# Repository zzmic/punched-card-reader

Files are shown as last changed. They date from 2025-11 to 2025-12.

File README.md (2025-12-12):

# punched-card-reader
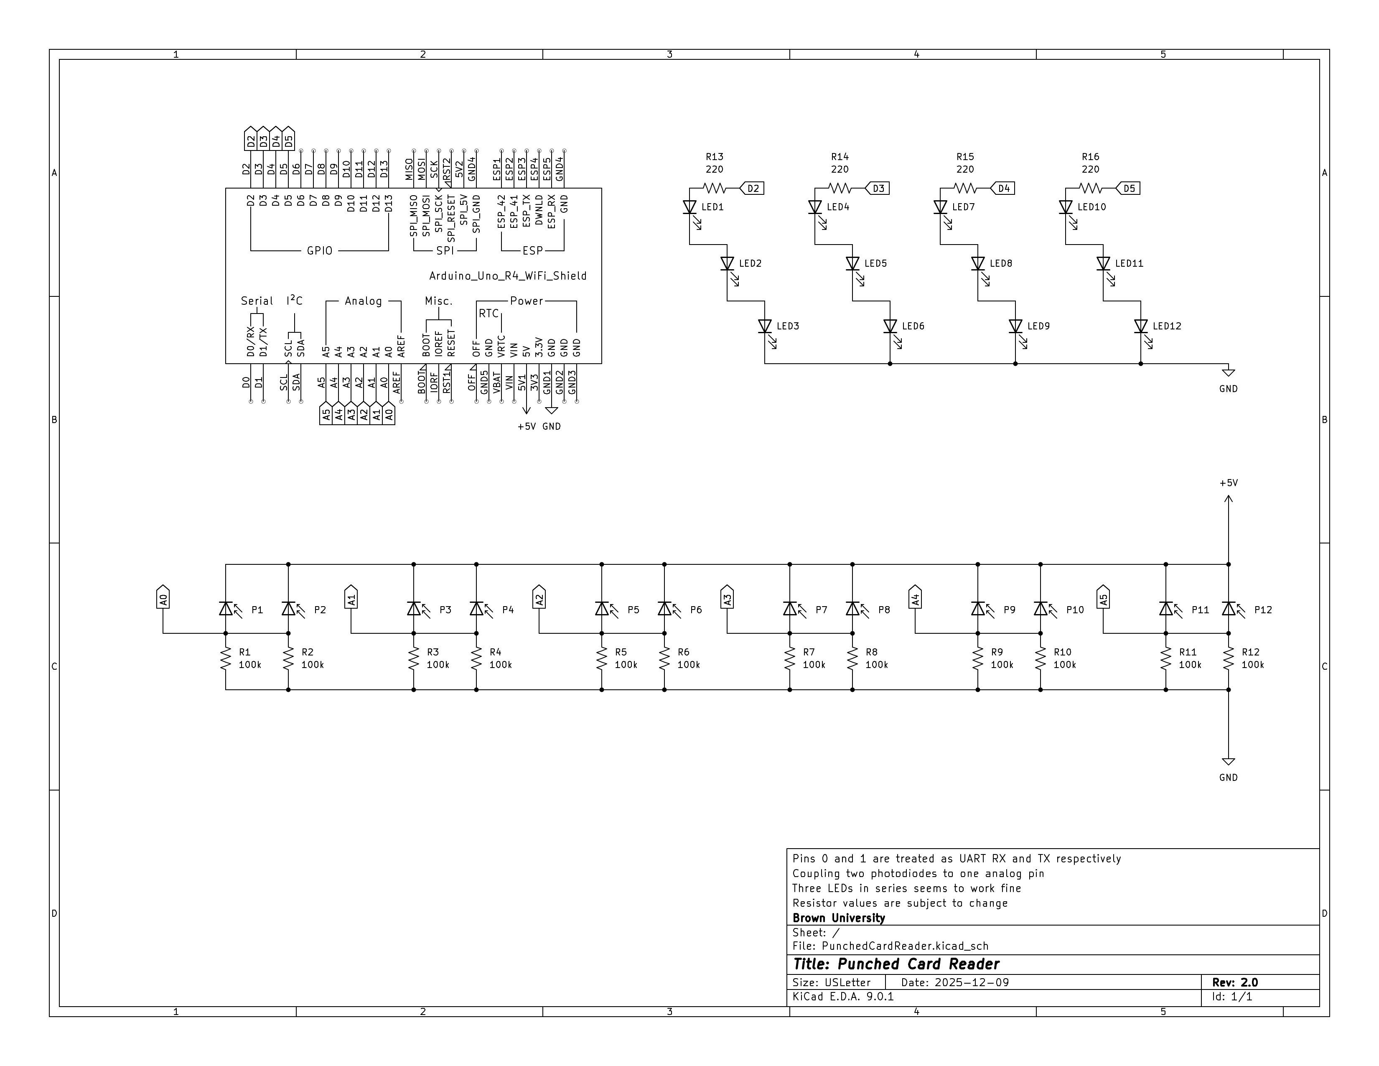
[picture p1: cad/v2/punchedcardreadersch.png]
Punched Card Reader Schematic


## Overview
This project is an Arduino‑based punched card reader that optically senses holes in punched cards and streams the decoded information via serial communication. It is intended to illustrate operating-system and low‑level I/O concepts by recreating the characteristics of historical slow peripheral devices.

## Group Members
- Yi Lyo
- Patrick McCann
- Alexander Thaep
- Zhiwen "Michael" Zheng

## Specifications
```
Punched Card Diameters
->  Length: 18.7325cm
->  Width: 8.255cm
->  Bits: 12 * 80 = 960b

Punched Card Reader:
->  Read start detected with an LED indicating the presence of a card
->  Notify card read start over serial
->  Starts with all LEDs off
->  Sampling Branch @ 1kHz:
  ->  Samples with LEDs off
  ->  Samples with LEDs on
  ->  Difference above a threshold comprises a sample of either 1 or 0
->  Reads 12 bits no more than 80 times and emits at most 16-bit words over serial
->  Read end detected with an LED indicating the absence of a card
->  Notify card read end over serial
```

## CAD
We have created some preliminary CAD prototypes just to virtually explore the physical design of our system. These files, in `.obj`, `.stl`, and `.f3z` formats, can be found in the respective folders according to their versions.

## Project Directory Hierarchy
```
.
├── arduino/                  # Arduino files for various sketches.
│   ├── PhotodiodeReadTest/   # Arduino sketch directory for testing photodiode readings.
│   └── punchedCardReader/    # Arduino sketch directory for the punched card reader ("The Implementation").
│   └── PunchcardReaderDraft/ # Early draft of the punched card reader Arduino sketch.
├── cad/                      # CAD files for prototype designs.
│   └── v1/                   # V1 prototype CAD files.
│   └── v2/                   # V2 prototype CAD files.
├── dafny/v1                  # Dafny verification files.
├── punchcard-generator/      # Punched card generator utility.
├── serial-reader/            # Serial reader utility for reading data from the punched card reader.
└── sim/                      # Simulation files.
    └── test-cards/           # Sample punched card files for testing the simulation.
```

## Hardware Requirements
- [Arduino® UNO R4 WiFi Board](https://store-usa.arduino.cc/products/uno-r4-wifi)

## Cloning the Repository
To clone the repository, use the following command:
```bash
git clone https://github.com/zzmic/punched-card-reader.git
```

## Arduino IDE Setup
The easiest way to set up the environment for compiling and uploading the Arduino sketches is to use the [Arduino IDE](https://www.arduino.cc/en/software/).
1. [Install](https://support.arduino.cc/hc/en-us/articles/360019833020-Download-and-install-Arduino-IDE) the Arduino IDE on a local machine.
2. Connect the Arduino® UNO R4 WiFi board to the local machine via a cable.
3. Open the Arduino IDE.
4. In the Arduino IDE, navigate to `Tools` > `Board` > `Board Manager...`, search for `Arduino UNO R4 WiFi`, and install the board core.
5. Navigate to `File` > `Open...`, and open the `arduino/punchedCardReader/punchedCardReader.ino` file from the cloned repository.
6. In the Arduino IDE, navigate to `Tools` > `Port`, and select the port corresponding to the connected Arduino® UNO R4 WiFi board.
7. Set the baud rate of the serial monitor to `115200` by navigating to `Tools` > `Serial Monitor` and selecting `115200` from the dropdown menu at the top right of the serial monitor window.
8. Click the `Upload` button (right arrow icon) in the Arduino IDE to compile and upload the sketch to the Arduino board.

## Unit Testing
Unit tests for the punched card reader are located in `arduino/punchedCardReader/unitTests.h` and `arduino/punchedCardReader/unitTests.ino`.
To run these tests, first enable unit testing and testing modes by uncommenting the `#define UNIT_TESTING` macro in `arduino/punchedCardReader/punchedCardReader.ino`.
After doing so, compiling and uploading the sketch to the Arduino board will automatically execute the `runUnitTests()` function within the `setup()` phase.
The test results, showing pass/fail status for the photodiode driver, card processor, and stream processor modules, are displayed on the serial monitor, with a clean run ending with the messages `All photodiode driver unit tests passed :)`, `All card processor unit tests passed :)`, and `All Hollerith unit tests passed :)`.
The testing framework uses mock functions defined in `arduino/punchedCardReader/testUtils.ino`, such as `evenLEDsOn` and `sendPunchReading`, which are activated by the `#define TESTING` macro.
These mocks intercept hardware calls to set state flags (e.g., `evenLEDsOnCalled`), enabling the unit tests to verify that the correct hardware control logic runs without requiring physical interaction, though the board must be connected and the sketch uploaded.

## Integration Testing
Integration tests for the punched card reader can be found at `arduino/punchedCardReader/softwareIntegrationTests.h` and `arduino/punchedCardReader/softwareIntegrationTests.ino`.
To run the integration tests, first enable integration testing and testing modes by uncommenting the `#define SOFTWARE_INTEGRATION_TESTING` macro in `arduino/punchedCardReader/punchedCardReader.ino`.
After doing so, compiling and uploading the sketch to the Arduino board drives the timer-based test harness that feeds a scripted sequence of sensor readings (simulating the card text `};\n`) into the system at each time step.
The harness invokes `checkMessages()` on each time step to compare the expected LED control, punch-reading generation, column/byte transmission, and card-end signaling against the actual mocked calls.
Results are printed to the serial monitor; any mismatch includes the expected and actual values, while a clean run ends with the message `finished software integration test (if only '};\n' was printed out, it passed)`.
The integration tests reuse the mock interfaces in `arduino/punchedCardReader/testUtils.ino`, such as `evenLEDsOn` and `sendPunchReading`, allowing the tests to validate the full sensing-to-streaming pipeline without requiring physical interaction, though the board must be connected and the sketch uploaded.

## Appendix A: Makefile Usage for Arduino Sketches through Arduino CLI (Optional)
Alternatively, to compile and upload Arduino sketches to the Arduino® UNO R4 WiFi board, ensure that [Arduino CLI](https://arduino.github.io/arduino-cli/1.3/installation/) is installed and available in the system's PATH and that the [Arduino® UNO R4 WiFi board core](https://docs.arduino.cc/hardware/uno-r4-wifi/) is installed. More information about interacting with Arduino CLI can be found in its [official documentation](https://arduino.github.io/arduino-cli/1.3/).

The following make commands (`make help` for help) built on `arduino-cli` can be used.
- To list connected Arduino boards:
  ```bash
  make arduino-board-list
  ```
  Make sure to record the port of the connected Arduino® UNO R4 WiFi board (e.g., `/dev/ttyACM0` on Linux, `COM3` on Windows, or `/dev/cu.usbmodemXXXX` on macOS) for use with the `upload` commands.
- To update the local cache of available platforms and libraries:
  ```bash
  make arduino-core-update-index
  ```
- To install the core for the Arduino® UNO R4 WiFi board:
  ```bash
  make arduino-core-install
  ```
- To list installed/available cores:
  ```bash
  make arduino-core-list
  ```
- To compile the Arduino sketch specified in FILE:
  ```bash
  make arduino-compile FILE=<path-to-sketch>
  ```
- To compile and upload the compiled Arduino sketch specified in FILE to the Arduino board at PORT:
  ```bash
  make arduino-compile-and-upload FILE=<path-to-sketch> PORT=<serial-port>
  ```

## Appendix B: Build and Run the Punched Card Reader Simulation (Optional)
Before building the simulation, ensure that a compatible [GCC](https://gcc.gnu.org) compiler that [supports C++14 or later](https://gcc.gnu.org/projects/cxx-status.html#cxx14) is [installed](https://gcc.gnu.org/install/) and available in the system's PATH.

The simulation of the *early design* of the punched card reader is implemented in C++ and can be built and run using the provided `Makefile` (`make help` for help).
1. Run `make sim-build` to build the simulation.
2. Run `./sim/bin/main` to start the simulation in interactive mode (specify the `--binary-mode` flag for binary output mode).
3. "Insert" a card file containing an 80 (column) * 12 (row) grid, where each entry represents a punch (any character other than `.` and whitespace) or no punch (`.` or whitespace). Sample card files are available in the `sim/test-cards/` directory.
4. To exit the simulation, type `done` when prompted for the next card file path. Otherwise, more card files can be input to continue the simulation.
5. Alternatively, do `make sim-test` (or `make sim-test-binary`) to run the simulation on *ALL* the test cards in the `sim/test-cards/` directory.

## Appendix C: Verification with Dafny (Optional)
The Dafny files in the `dafny/v1/` directory *aim* to formally verify, at the algorithmic level, the correctness of the logic of core components based on the *early design* of the punched card reader using [the Dafny programming and verification language](https://dafny.org).
The Dafny implementation does not directly interact with the Arduino hardware or the Arduino framework; instead, it focuses solely on verifying the algorithms and data structures used in the punched card reader's software design.
Due to time constraints, the Dafny programs might not comprehensively cover the up-to-date punched card reader's functionality (i.e., we do *not* claim full verification of the entire system), but they still serve as a useful tool for spotting potential issues we might encounter during system design, specification, and implementation.

To verify the Dafny programs, ensure that [the Dafny binary build or the VSCode extension for Dafny (Dafny VSCode)](https://dafny.org/latest/Installation) is installed.
If using the command line, run the following command from the project's root directory:
```bash
dafny verify dafny/v1/*.dfy
```

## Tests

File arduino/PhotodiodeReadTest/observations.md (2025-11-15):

When the switch is open (IR LED off), the reading is 22–23.

When the switch is closed (IR LED on), the reading is 1018–1019.

When the switch is closed (IR LED on) and a piece of paper (standard letter-
size printer paper folded in half) is inserted between the diodes, the reading 
is 400–500.

The reading drops dramatically when the diodes are moved further apart or 
moved out of alignment. The reading can be tuned by changing the value of the 
resistor attached to the photodiode; a higher resistor value results in 
larger readings. For the reader, we will likely choose a resistor value around 
100 kΩ, though this will need to be tested with the actual reader assembly.

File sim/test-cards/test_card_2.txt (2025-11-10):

################################################################################
................................................................................
################################################################################
................................................................................
################################################################################
................................................................................
################################################################################
................................................................................
################################################################################
................................................................................
################################################################################
................................................................................

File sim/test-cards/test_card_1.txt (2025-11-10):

#.#.#.#.#.#.#.#.#.#.#.#.#.#.#.#.#.#.#.#.#.#.#.#.#.#.#.#.#.#.#.#.#.#.#.#.#.#.#.#.
.#.#.#.#.#.#.#.#.#.#.#.#.#.#.#.#.#.#.#.#.#.#.#.#.#.#.#.#.#.#.#.#.#.#.#.#.#.#.#.
################################################################################
................................................................................
#...............................................................................
.#..............................................................................
..#.............................................................................
...#............................................................................
....#...........................................................................
.....#..........................................................................
......#.........................................................................
.......#........................................................................

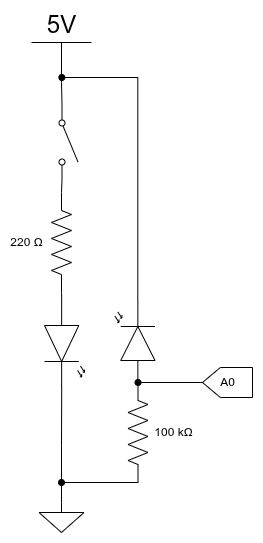
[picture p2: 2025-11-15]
arduino/PhotodiodeReadTest/circuit.png

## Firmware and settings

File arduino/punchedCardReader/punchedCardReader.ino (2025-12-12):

// #define UNIT_TESTING
// #define SOFTWARE_INTEGRATION_TESTING
// #define HARDWARE_TESTING

#include <Arduino.h>
#include <FspTimer.h>

#if defined(UNIT_TESTING) || defined(SOFTWARE_INTEGRATION_TESTING)
  #define TESTING
#endif

#include "sensors.h"
#include "photodiodeDriver.h"
#include "cardProcessor.h"
#include "streamProcessor.h"
#include "computer.h"
#include "wdt.h"

#ifdef TESTING
  #include "testUtils.h"
#endif // TESTING
#ifdef UNIT_TESTING
  #include "unitTests.h"
#endif // UNIT_TESTING
#ifdef SOFTWARE_INTEGRATION_TESTING
  #include "softwareIntegrationTests.h"
#endif // SOFTWARE_INTEGRATION_TESTING

/**
 * Constants and variables for buffering serial output.
 */
#define BUF_LEN 128
volatile char buffer[BUF_LEN];
volatile int start = 0;
volatile int end = 0;

/**
 * Timer object and testing flags.
 */
FspTimer myTimer;
volatile bool finished_software_integration_tests;
volatile char curReading[12];

/**
 * Timer interrupt service routine (ISR).
 *
 * This function is called at a fixed rate to read sensor data and process it.
 *
 * @param p_args Pointer to timer callback arguments (not used).
 */
static void timerISR(timer_callback_args_t *p_args) {
  SensorReading curReading = readSensors();
  sendSensorReading(curReading);

  #ifdef SOFTWARE_INTEGRATION_TESTING
    if (!finished_software_integration_tests && checkMessages()) {
      finished_software_integration_tests = true;
    }
  #endif
}

/**
 * Setup function.
 */
void setup() {
  // put your setup code here, to run once:
  Serial.begin(115200);
  while (!Serial);

  initSensors();
  initPhotodiodeDriver();
  initCardProcessor();
  initStreamProcessor();

  #ifdef UNIT_TESTING
  runUnitTests();
  #endif // UNIT_TESTING

  // Init and pet WDT to kick it off
  #ifndef UNIT_TESTING
  initWDT();
  petWDT();
  #endif // UNIT_TESTING

  // Define timer type and find an available channel
  uint8_t timerType = GPT_TIMER;
  int8_t channel = FspTimer::get_available_timer(timerType);

  if (channel < 0) {
    Serial.println("No free GPT timer available");
    while (1);
  }

  // Configure the timer
  // Parameters: mode, type, channel, frequency (Hz), dutyCycle (for PWM, 50% for periodic), callback function
  bool ok = myTimer.begin(TIMER_MODE_PERIODIC, GPT_TIMER, channel, 4000, 50.0, &timerISR); // complete 4-state cycle at 1 kHz frequency

  if (!ok) {
    Serial.println("Timer initialization failed");
    while (1);
  }

  myTimer.setup_overflow_irq();
  // Open the timer (necessary for the R4)
  myTimer.open();

  // Start the timer
  myTimer.start();
}

/**
 * Main loop function.
 */
void loop() {
  noInterrupts();
  bool hasData = (start != end);
  char b = 0;
  if (hasData) {
    b = buffer[start];
    start = (start + 1) & 0x7F;
  }
  interrupts();

  if (hasData) {
    Serial.print(b);
  }

  #ifdef SOFTWARE_INTEGRATION_TESTING
  if (finished_software_integration_tests) {
    Serial.println("finished software integration test (if only '};<newline>' was printed out, it passed)");
    while(1);
  }
  #endif

  #ifdef HARDWARE_TESTING
  for (int i = 0; i < 12; i++) {
    Serial.print(curReading[i]);
  }
  Serial.println("");
  #endif
}

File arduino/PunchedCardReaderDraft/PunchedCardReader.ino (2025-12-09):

#include "Arduino.h"
#include "PunchedCardReader.h"

/**
 * Constants for setting up the GPT3 timer interrupt.
 *
 * c_TIMER_INT: The interrupt number for GPT3.
 * c_PERIOD_MILLISECONDS: The period of the timer interrupt in milliseconds.
 * c_COUNTER: The counter value calculated based on the desired period and clock settings.
 */
const unsigned int c_TIMER_INT = 31;
const unsigned int c_PERIOD_MILLISECONDS = 5;
//  period in ms * 1/1000 sec/ms (48 * 1000 * 1000) cycles/sec * (1/1024) scaling factor
const uint32_t c_COUNTER = (c_PERIOD_MILLISECONDS * (48 * 1000 * 1000 / 1024)) / (1000);

/**
 * Timer interrupt service routine (ISR) for handling GPT3 interrupts.
 */
void timerISR() {
  // stop the GPT3 counter
  R_GPT3->GTCR_b.CST = 0;

  SensorReadings cur_reading = readSensors();
  sendSensorReading(cur_reading);

  // Set up the next noteISR by setting a counter value and turning on GPT3 counter
  R_GPT3->GTPR = c_COUNTER;
  R_ICU->IELSR[c_TIMER_INT] = (0x075 << R_ICU_IELSR_IELS_Pos);
  R_GPT3->GTCR_b.CST = 1;

  // Clear any pending flags
  // MCU side
  R_ICU->IELSR_b[c_TIMER_INT].IR = 0;
  // Clear the pending interrupt on the CPU side
  NVIC_ClearPendingIRQ((IRQn_Type) c_TIMER_INT);
}

void setup() {
  Serial.begin(9600);
  // initialize digital pin LED_BUILTIN as an output.
  pinMode(LED_BUILTIN, OUTPUT);

  initSensors();
  initPhotodiodeDriver();
  initCardProcessor();
  initStreamProcessor();

  // Enable GPT peripheral
  R_MSTP->MSTPCRD_b.MSTPD6 = 0;
  // Make sure the count isn't started
  R_GPT3->GTCR_b.CST = 0;
  // Make sure nobody else can start the count (see 22.2.5 and 22.2.6)
  R_GPT3->GTSSR = (1 << R_GPT0_GTSSR_CSTRT_Pos); // only started w/ software
  R_GPT3->GTPSR = (1 << R_GPT0_GTPSR_CSTOP_Pos); // only stopped w/ software
  // Divide the GPT3 clock
  R_GPT3->GTCR = R_GPT3->GTCR & ~(0b111 << 24) | (0b101 << 24);
  // Disable GPT interrupt on ICU for now
  R_ICU->IELSR[c_TIMER_INT] = 0;
  // Use the Arm CMSIS API to enable CPU interrupts
  R_ICU->IELSR[c_TIMER_INT] = (0x075 << R_ICU_IELSR_IELS_Pos); // interrupt enabled on GPT3 overflow

  NVIC_SetVector((IRQn_Type) c_TIMER_INT, (uint32_t) &timerISR); // set vector entry to our handler
  NVIC_SetPriority((IRQn_Type) c_TIMER_INT, 13); // Priority lower than Serial (12)
  NVIC_EnableIRQ((IRQn_Type) c_TIMER_INT);

  // kick off first noteISR by setting a counter value and turning on the counter
  R_GPT3->GTPR = 1;
  R_GPT3->GTCR_b.CST = 1;
}

void loop() {}

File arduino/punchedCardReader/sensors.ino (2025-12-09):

const int c_ANALOG_PINS[6] = {A0, A1, A2, A3, A4, A5};
// const int c_DIGITAL_PINS[12] = {
//     D2, D3, D4, D5, D6, D7, D8, D9, D10, D11, c_SENSE_EMITTER_PIN};
// const int c_EVEN_PINS[6] = {D0, D2, D4, D6, D8, D10};
// const int c_ODD_PINS[6] = {D1, D3, D5, D7, D9, D11};

/**
 * Write a value to a range of pins.
 *
 * @param start_addr Pointer to the start of the pin array.
 * @param end_addr Pointer to the end of the pin array.
 * @param value The value to write to each pin.
 */
void writePins(const int *start_addr, const int *end_addr, int value) {
  for (const int *pin = start_addr; pin != end_addr; ++pin) {
    digitalWrite(*pin, value);
  }
}

/**
 * Read values from a range of pins into a buffer.
 *
 * @param start_addr Pointer to the start of the pin array.
 * @param end_addr Pointer to the end of the pin array.
 * @param buffer Pointer to the buffer where readings will be stored.
 */
void readPins(const int *start_addr, const int *end_addr, int *buffer) {
  int *index = buffer;
  for (const int *pin = start_addr; pin != end_addr; ++pin) {
    *index++ = analogRead(*pin);
  }
}

/**
 * Print pin readings from a range of pins.
 *
 * @param start_addr Pointer to the start of the pin array.
 * @param end_addr Pointer to the end of the pin array.
 */
void printPins(const int *start_addr, const int *end_addr, int * /*buffer*/) {
  for (const int *pin = start_addr; pin != end_addr; ++pin) {
    Serial.print(analogRead(*pin));
    Serial.print(":");
  }
  Serial.println();
}

/**
 * Print the contents of a buffer.
 *
 * @param start_addr Pointer to the start of the buffer.
 * @param size Number of elements in the buffer.
 */
void printBuffer(const int *start_addr, size_t size) {
  for (const int *item = start_addr; item != start_addr + size; ++item) {
    Serial.print(*item);
    Serial.print(":");
  }
  Serial.println();
}

/**
 * Initialize sensor pins.
 */
void initSensors() {
    // for (int i = 0; i < EMITTER_PINS_COUNT; ++i) {
    //   pinMode(c_DIGITAL_PINS[i], OUTPUT);
    // }
    // pinMode(c_SENSE_EMITTER_PIN, INPUT);
    // writePins(c_DIGITAL_PINS, c_DIGITAL_PINS + EMITTER_PINS_COUNT, HIGH);
}

#ifndef SOFTWARE_INTEGRATION_TESTING
/**
 * Read sensor values and return a `SensorReading` struct.
 *
 * @return SensorReading containing the readings from the sensors.
 */
SensorReading readSensors() {
  SensorReading result;
  for (int i = 0; i < READ_PINS_COUNT; i++) {
    result.readings[i] = analogRead(c_ANALOG_PINS[i]);
  }
  return result;
}
#endif // SOFTWARE_INTEGRATION_TESTING

#ifndef TESTING
/**
 * Turn on even LEDs.
 */
void evenLEDsOn() {
  //writePins(c_EVEN_PINS, c_EVEN_PINS + HALF_EMITTER_PINS_COUNT, LOW);
}

/**
 * Turn off even LEDs.
 */
void evenLEDsOff() {
  //writePins(c_EVEN_PINS, c_EVEN_PINS + HALF_EMITTER_PINS_COUNT, HIGH);
}

/**
 * Turn on odd LEDs.
 */
void oddLEDsOn() {
  //writePins(c_ODD_PINS, c_ODD_PINS + HALF_EMITTER_PINS_COUNT, HIGH);
}

/**
 * Turn off odd LEDs.
 */
void oddLEDsOff() {
  //writePins(c_ODD_PINS, c_ODD_PINS + HALF_EMITTER_PINS_COUNT, LOW);
}
#endif // TESTING

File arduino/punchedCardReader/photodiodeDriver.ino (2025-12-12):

/**
 * Update the photodiode state machine based on the current state and sensor reading.
 *
 * @param curState The current state of the photodiode driver.
 * @param reading The current sensor reading from the photodiodes.
 * @return The updated state of the photodiode driver.
 */
FullPhotodiodeState updatePhotodiodeState(FullPhotodiodeState& curState, SensorReading& reading) {
  FullPhotodiodeState ret = curState;

  switch(curState.state) {
    /* 0-1 (the guard is always true). */
    case s_ALL_OFF:
    for (int i = 0; i < 6; i++) {
      ret.offVals[2 * i] = reading.readings[i];
      ret.offVals[(2 * i) + 1] = reading.readings[i];
    }
    ret.state = s_EVEN_ON;
    evenLEDsOn();
    break;

    /* 1-2 (the guard is always true). */
    case s_EVEN_ON:
    for (int i = 0; i < 6; i++) {
      ret.onVals[2 * i] = reading.readings[i];
    }
    ret.state = s_ODD_ON;
    evenLEDsOff();
    oddLEDsOn();
    break;

    /* 2-3 (the guard is always true). */
    case s_ODD_ON:
    for (int i = 0; i < 6; i++) {
      ret.onVals[(2 * i) + 1] = reading.readings[i];
    }
    ret.state = s_CALC;
    oddLEDsOff();
    break;

    /* 3-0 (the guard is always true). */
    case s_CALC:
    PunchReading punched;
    for (int i = 0; i < 12; i++) {
      punched.holes[i] = (curState.onVals[i] - curState.offVals[i]) > minDiff;
    }
    sendPunchReading(punched);
    ret.state = s_ALL_OFF;
    petWDT();
    #ifdef HARDWARE_TESTING
    for (int i = 0; i < 12; i++) {
      if (punched.holes[i]) {
        curReading[i] = '1';
      } else {
        curReading[i] = '0';
      }
    }
    #endif
    break;
  }

  return ret;
}

/**
 * The current state of the photodiode driver.
 *
 * It is declared as volatile since it may be modified in an interrupt context.
 */
volatile FullPhotodiodeState curPhotodiodeState;

/**
 * Initialize the photodiode driver.
 */
void initPhotodiodeDriver() {
  curPhotodiodeState.state = s_ALL_OFF;
  for (int i = 0; i < 12; i++) {
    curPhotodiodeState.offVals[i] = 0;
    curPhotodiodeState.onVals[i] = 0;
  }
}

#ifndef TESTING
/**
 * Send a sensor reading to the photodiode driver, updating its state.
 *
 * @param reading The punched reading to send.
 */
void sendSensorReading(SensorReading& reading) {
  FullPhotodiodeState curState;
  curState.state = curPhotodiodeState.state;
  for (int i = 0; i < 12; i++) {
    curState.onVals[i] = curPhotodiodeState.onVals[i];
    curState.offVals[i] = curPhotodiodeState.offVals[i];
  }

  FullPhotodiodeState nextState = updatePhotodiodeState(curState, reading);

  curPhotodiodeState.state = nextState.state;
  for (int i = 0; i < 12; i++) {
    curPhotodiodeState.onVals[i] = nextState.onVals[i];
    curPhotodiodeState.offVals[i] = nextState.offVals[i];
  }
}
#endif TESTING

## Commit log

2025-10-14 Preliminarily implement a TLA+ specification that models the punched card reader
    [PunchedCardSpec.cfg]
2025-10-14 Update `tlaplus-specification/cleanup.sh` and `tlaplus-specification/.gitignore`
    [PunchedCardSpec.cfg]
2025-10-15 1. Progress on the TLA+ specification (that models the punched card reader)
    2. Compile (recompile) `project-proposal/project_proposal.tex` to update `project-proposal/project_proposal.pdf`
    [PunchedCardSpec.cfg]
2025-10-16 Progress on the TLA+ specification (that models the punched card reader)
    [PunchedCardSpec.cfg]
2025-11-07 1. Initialize `PunchedCardReader/` with `PunchedCardReader/Blink.ino` for testing whether the on-board LED works
    2. Update `README.md`
2025-11-07 1. `mkdir docs && mv project-proposal tlaplus-specification docs`
    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
    [PunchedCardSpec.cfg]
2025-11-07 1. Add `Makefile`
    2. Add `PunchedCardReader/Calibration.ino` for calibrating sensor input
    3. Update `README.md`
2025-11-10 Primarily revise the simulator driver implemenation
2025-11-10 added cad files of punched card prototype
2025-11-10 Revise the simulator implementation to (1) print the data for each column while reading (2) support the binary mode to output binary data instead
2025-11-10 Fix the command-line-argument parsing logic
    [main.cpp]
2025-11-12 `mv docs/tlaplus-specification docs/tlaplus-specs`
    [PunchedCardSpec.cfg]
2025-11-12 Preliminarily implement the `PhotodiodeDriver` module
    [PunchedCardSpec.cfg]
2025-11-12 Revise the previously implemented modules
    [PunchedCardReader.cfg]
2025-11-12 Revise the formatting of column-data printing
2025-11-12 1. Revise the formatting of column-data printing
    2.Revise the inline documentation in `sim/PunchedCardReaderSimulator.*`
2025-11-14 Move `docs/tlaplus-specs` out of the repo
    [PunchedCardReader.cfg]
2025-11-17 Revert commit 27a9906 to (temporarily) preserve the usage of `Makefile`
    This reverts commit 27a9906a50a7fb536e38f2d076c62d148f2c4199.
    [PunchedCardReader.ino]
2025-11-17 Update `README.md` to reflect the Arduino sketch directory for testing photodiode readings
2025-11-17 feat: card processor state machine module for arduino (plus tests)
2025-11-19 Implement the Dafny module of the photodiode driver
2025-11-25 Configure P102 analog pin and other pins
2025-11-25 Implement hardware test for IR LEDs
2025-12-01 Update photodiode resistor value and upload current hardware test code
    [PunchedCardReader.kicad_sch]
2025-12-01 Attempt to read digital pin 13 as anlog
2025-12-02 Implement pre-read on/off calibration read
    [PunchedCardReader.kicad_sch]
2025-12-02 1. Preliminarily implement `arduino/punchedCardReader/sensors.*`
    2. Add include guards in the header files in `arduino/punchedCardReader/*`
2025-12-02 1. "Revert" `sensorReading readSensors(punchReading punched)` to `sensorReading readSensors()`
    2. Fix the include guards for compilation (linking)
    [punchedCardReader.ino, sensors.h, sensors.ino]
2025-12-02 Replace the identifiers of the enums and structs in `arduino/punchedCardReader/*` with their capitalized counterparts in order to respect the Pascal-case naming convention
    [cardProcessor.ino, photodiodeDriver.ino, punchedCardReader.ino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]
2025-12-02 Revise the Makefile target `arduino-upload` to `arduino-compile-and-upload` with changes in its recipe
2025-12-08 adapt arduino code for hollerith and 12 sensors
2025-12-08 Add some inline comments for `arduino/punchedCardReader/*`
2025-12-08 Continue adding inline comments for `arduino/punchedCardReader/*`
2025-12-08 adapted software integration tests for 12 sensors and hollerith
2025-12-08 Fix stupid schematic blunder
    [PunchedCardReader.kicad_sch]
2025-12-09 Fill out sensors write to LEDs on/off
2025-12-09 Remove calibrate() and hardwareTest()
2025-12-09 Implement circular buffer for buffered UART send
2025-12-09 testing out better timer
2025-12-09 Add new schematic for reader circuit
    [PunchedCardReader.kicad_sch]
2025-12-09 first attempt at making timer period faster
2025-12-09 Update the documentation of `arduino/punchedCardReader/*`
2025-12-11 Update the instructions for setting up the Arduino IDE, along with other changes, in `README.md`
2025-12-11 Add photodiode driver state variable initialization
2025-12-11 Implement watchdog timer
2025-12-11 Add the instruction for setting the baud rate of the IDE’s serial monitor, along with other changes, in `README.md`
2025-12-11 Replace hardcoded magic values with named constants
    [streamProcessor.ino]
2025-12-11 Add interrupt disabling (and later enabling) to protect the ring-buffer updates from race conditions
2025-12-12 Fix minor (major?) bad index into memory
    [photodiodeDriver.ino]
2025-12-12 rename timerISR2 just timerISR
